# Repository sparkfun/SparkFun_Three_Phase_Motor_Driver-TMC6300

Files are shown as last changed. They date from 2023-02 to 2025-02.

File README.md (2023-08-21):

SparkFun 3-Phase BLDC Motor Driver - TMC6300
========================================

SparkFun 3-Phase BLDC Motor Driver - TMC6300 (https://www.sparkfun.com/products/21867)

[*SparkFun 3-Phase BLDC Motor Driver - TMC6300 (ROB-21867)*](https://www.sparkfun.com/products/21867)

The TMC6300 from [ADI + Trinamic](https://www.trinamic.com/) is a powerful and easy to use three phase motor driver that was designed to control our [Brushless Gimbal Motor](https://www.sparkfun.com/products/20441). However, it can be used to control any 3-phase [BLDC](https://en.wikipedia.org/wiki/Brushless_DC_electric_motor "brushless DC") or [PMSM](https://en.wikipedia.org/wiki/Synchronous_motor#Permanent-magnet "permanent magnet synchronous motor") motor with up to 2A (1.4A<sub>RMS</sub>) of total drive current. Separate high-side and low-side control of the three half-bridges allows for incredible control of each phase of the [motor commutation](https://fab.cba.mit.edu/classes/865.21/topics/power_electronics/commutation/#bldc-commutation). The driver also provides temperature and short circuit protections; and a diagnostic output to indicate system faults. With a 1.8V regulated power output and an operating voltage down to 2V, the TMC6300 is suitable for low-power microcontroller and battery powered designs (min. 2 AA/NiMh cells, or 1-2 Li-Ion cells).

Our board layout has been designed with the LEDs and labels facing up, IC down. This allows the thermal pad on the board to be access if cooling is required. Additionally, the breakout pins are specially aligned to fit perfectly onto a breadboard and hold the headers more perpendicular to facilitate assembly.

Controlling 3-phase motors is not trivial and this board requires 6 PWM signals to fully control one motor. We've found the [*Arduino Simple Field Oriented Control*](https://docs.simplefoc.com/) library to work well with the board; however, there are some hadware limitations such as [supported microconrollers for `6PWM Mode`](https://docs.simplefoc.com/microcontrollers#supported-microcontrollers). With additional considerations, for integrating [position sensors](https://docs.simplefoc.com/position_sensors) into the feedback control loop.

Repository Contents
-------------------

* **[/docs](/docs/)** - Online documentation files
    * [arduino_examples](/docs/arduino_examples/) - Example code
    * [board_files](/docs/board_files/) - Files for the product design
            * [Eagle design files](/docs/board_files/eagle_files.zip) (.zip)
            * [Schematic](/docs/board_files/schematic.pdf) (.pdf)
            * [Dimensions](/docs/board_files/dimensions.pdf) (.pdf)
    * [component_documentation](/docs/component_documentation/) - Datasheets for hardware components
    * [img/hookup_guide/](/docs/img/hookup_guide/) - Images for hookup guide documentation
* **[/Hardware](/Hardware/)** - Eagle design files (.brd, .sch)

Documentation
--------------
* **[Hookup Guide (mkdocs)](http://docs.sparkfun.com/SparkFun_Three_Phase_Motor_Driver-TMC6300/)** - Hookup guide for the TMC6300 Motor Driver hosted by GitHub pages.

*Need to download or print our hookup guide?*

* [Print *(Print to PDF)* from Single-Page View](http://docs.sparkfun.com/SparkFun_Three_Phase_Motor_Driver-TMC6300/single_page)
* [Download PDF](http://docs.sparkfun.com/SparkFun_Three_Phase_Motor_Driver-TMC6300/board_files/hookup_guide.pdf) *(Beta - Mostly works, but some attributes may be broken.)*

Product Variants
----------------
* [ROB-21867](https://www.sparkfun.com/products/21867)- v1.0, Initial Release

Version History
---------------
* [v01](https://github.com/sparkfun/SparkFun_Three_Phase_Motor_Driver-TMC6300/releases/tag/v10) - Initial Release

License Information
-------------------

This product is _**open source**_! 

Please review the LICENSE.md file for license information. 

If you have any questions or concerns about licensing, please contact technical support on our [SparkFun forums](https://forum.sparkfun.com/viewforum.php?f=152).

Distributed as-is; no warranty is given.

- Your friends at SparkFun.

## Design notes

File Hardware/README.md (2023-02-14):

SparkFun <PRODUCT NAME> Design Files
=====================================

The .sch and .brd files hare are Eagle CAD schematic and PCB design files from SparkFun Electronics.
A freeware version of Autodesk Eagle can be found [here](https://www.autodesk.com/products/eagle/free-download).

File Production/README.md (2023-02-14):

SparkFun <PRODUCT NAME> Production Files
=========================================

These are the production files SparkFun uses for printing PCBs.

License Information
-------------------
This product is open source! 

The hardware is released under [Creative Commons ShareAlike 4.0 International](https://creativecommons.org/licenses/by-sa/4.0/).

Please use, reuse, and modify these files as you see fit. Please maintain attribution to SparkFun Electronics and release anything derivative under the same license.

Distributed as-is; no warranty is given.

- Your friends at SparkFun.

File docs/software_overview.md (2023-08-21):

---
icon: simple/arduino
---

## Arduino IDE
!!! tip
	For first-time users, who have never programmed before and are looking to use the Arduino IDE, we recommend beginning with the <a href="https://www.sparkfun.com/products/15631">SparkFun Inventor's Kit (SIK)</a>, which is designed to help users get started programming with the Arduino IDE.

Most users may already be familiar with the Arduino IDE and its use. However, for those of you who have never heard the name *Arduino* before, feel free to check out the [Arduino website](https://www.arduino.cc/en/Guide/HomePage). To get started with using the Arduino IDE, check out our tutorials below:

<table class="pdf" style="border-style:none" align="center">
	<tr>
		<td align="center">
			<a class="thumb" href="https://learn.sparkfun.com/tutorials/50">
				What is an Arduino?
				<h3 class="title">What is an Arduino?</h3>
			</a>
		</td>
		<td align="center">
			<a class="thumb" href="https://learn.sparkfun.com/tutorials/61">
				Installing Arduino IDE
				<h3 class="title">Installing Arduino IDE</h3>
			</a>
		</td>
		<td align="center">
			<a class="thumb" href="https://learn.sparkfun.com/tutorials/15">
				Installing an Arduino Library
				<h3 class="title">Installing an Arduino Library</h3>
			</a>
		</td>
		<td align="center">
			<a class="thumb" href="https://learn.sparkfun.com/tutorials/1265">
				Installing Board Definitions in the Arduino IDE
				<h3 class="title">Installing Board Definitions in the Arduino IDE</h3>
			</a>
		</td>
	</tr>
</table>

<div class="grid cards" markdown align="center">

-   <a href="https://learn.sparkfun.com/tutorials/50"><figure markdown>
	What is an Arduino?
	</figure>

	---

	**What is an Arduino?**</a>

-   <a href="https://learn.sparkfun.com/tutorials/61"><figure markdown>
	Installing the Arduino IDE
	</figure>

	---
	
	**Installing the Arduino IDE**</a>

-   <a href="https://learn.sparkfun.com/tutorials/15"><figure markdown>
	Installing an Arduino Library
	</figure>

	---
	
	**Installing an Arduino Library**</a>

-   <a href="https://learn.sparkfun.com/tutorials/1265"><figure markdown>
	Installing Board Definitions in the Arduino IDE
	</figure>

	---
	
	**Installing Board Definitions in the Arduino IDE**</a>
</div>

??? tip "Need help setting up the RedBoard Plus?"
	### RedBoard Plus
	The following instructions should help users get started with the RedBoard Plus. For more information about the board, please check out our hookup guide below:

	<figure markdown>
	RedBoard Plus Hookup Guide (https://learn.sparkfun.com/tutorials/1758)
	<figcaption markdown>[**RedBoard Plus Hookup Guide**](https://learn.sparkfun.com/tutorials/1758)</figcaption>
	</figure>

	#### CH340 Driver
	Users will need to install the appropriate driver for their computer to recognize the serial-to-UART chip on their board/adapter. Most of the latest operating systems will recognize the CH340C chip on the board and automatically install the required driver.

	*To manually install the CH340 driver on their computer, users can download it from the [WCH website](http://www.wch-ic.com/products/CH340.html?). For more information, check out our [How to Install CH340 Drivers Tutorial](https://www.sparkfun.com/ch340).*

	<figure markdown>
	How to Install CH340 Drivers (https://learn.sparkfun.com/tutorials/908)
	<figcaption markdown>[**How to Install CH340 Drivers**](https://learn.sparkfun.com/tutorials/908)</figcaption>
	</figure>

	#### Arduino IDE
	When selecting a board to program in the Arduino IDE, users should select the **Arduino Uno** from the **Tools** drop-down menu _(_i.e. **Tools** > **Board** > **Arduino AVR Boards** > **Arduino Uno**)_.

	<figure markdown>
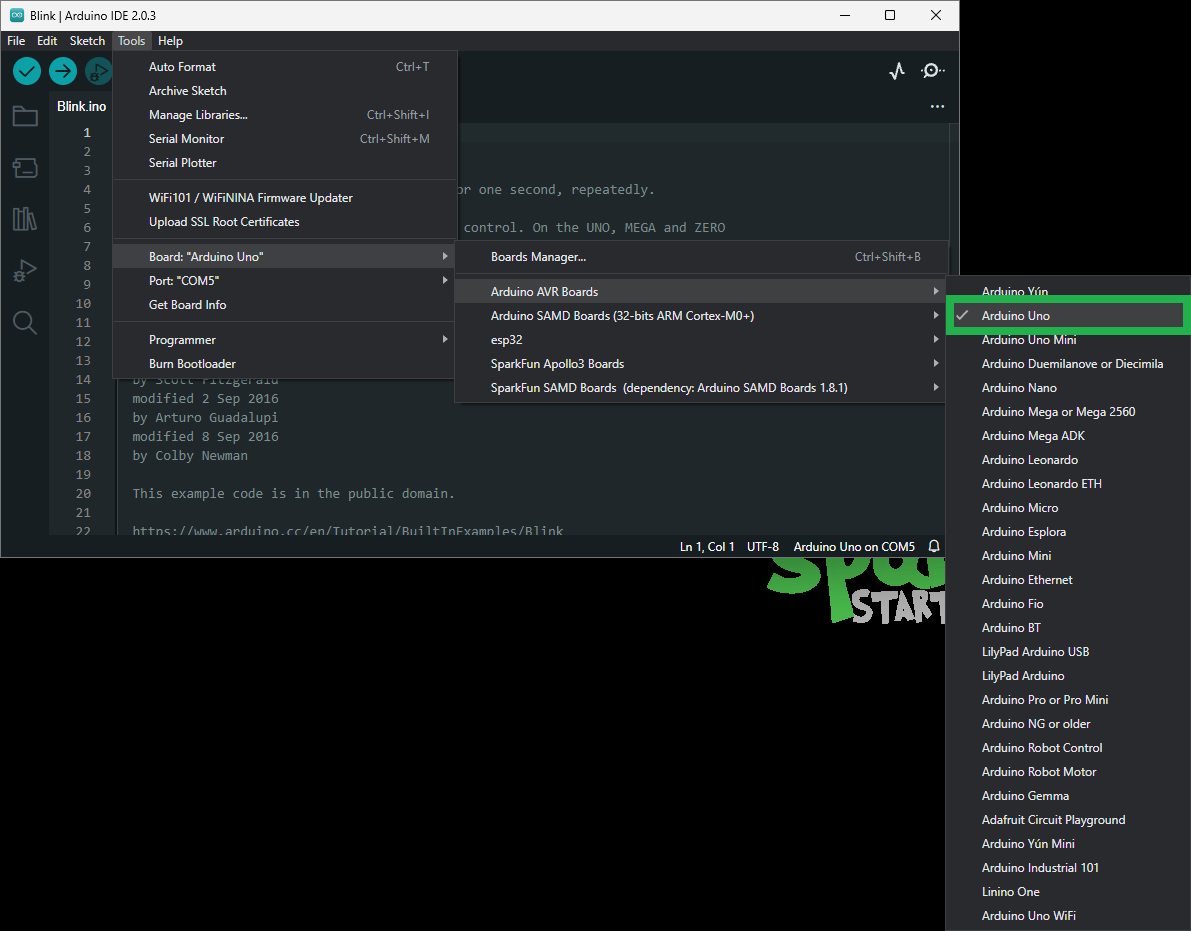
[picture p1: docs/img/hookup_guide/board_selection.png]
	
	<figcaption markdown>Select the **Arduino Uno** from the Tools drop-down menu in the Arduino IDE.</figcaption>
	</figure>

	??? info "Arduino IDE 2.x.x - *Alternative Method*"
		In the newest version of the Arduino IDE 2.`x`.`x`, users can also select their board (*green*) and port (*blue*) from the `Select Board & Port` dropdown menu (*yellow*).

		<figure markdown>
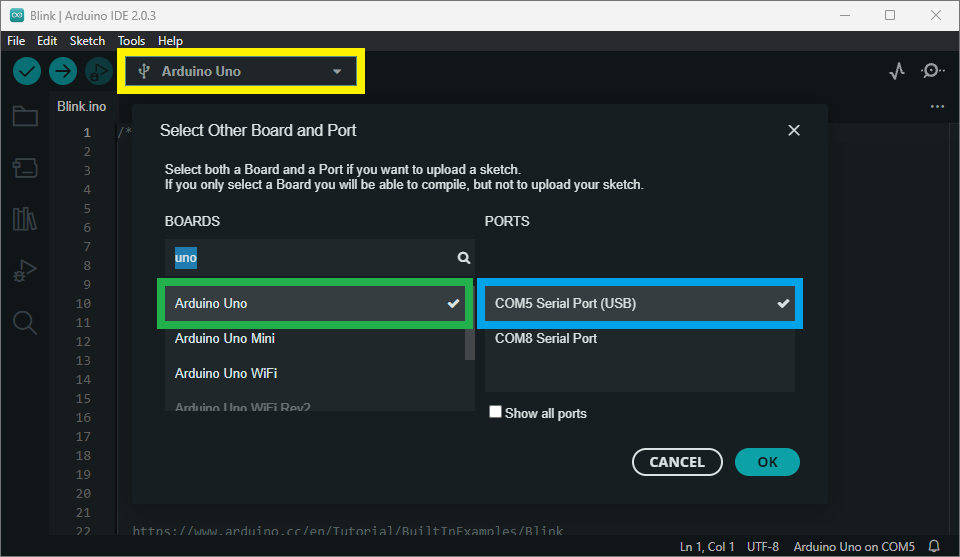
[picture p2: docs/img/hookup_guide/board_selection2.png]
		
		<figcaption markdown>Selecting the **Arduino Uno** and **COM5** port from the **Select Board & Port** drop-down menu in the Arduino IDE (v2.0.3).</figcaption>
		</figure>

## SimpleFOClibrary
The [Simple Field Oriented Control Library](https://github.com/simplefoc/Arduino-FOC) can be installed from the library manager in the Arduino IDE.

<figure markdown>
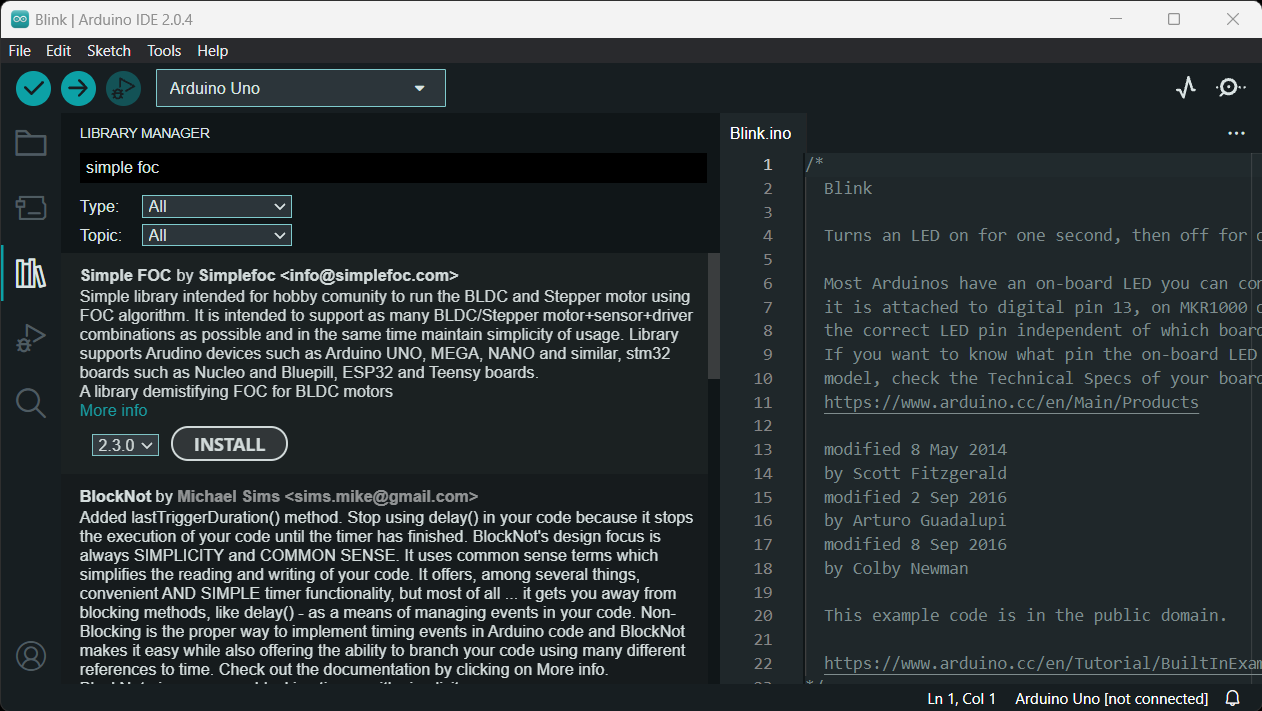
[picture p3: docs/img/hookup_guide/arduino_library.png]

<figcaption markdown>SimpleFOClibrary in the library manager of the Arduino IDE.</figcaption>
</figure>

??? tip "Arduino IDE *(v1.x.x)*"
	In the Arduino IDE v1.x.x, the library manager will have the following appearance for the SimpleFOC library:

	<figure markdown>
	Click to enlarge
	<figcaption markdown>SimpleFOClibrary in the library manager of the Arduino IDE (v1.x.x).</figcaption>
	</figure>

This library utilizes a motor control scheme called field oriented control (FOC), which can utilize a feedback control loop to drive a motor with a higher power efficiency and precision characteristics, like evenly distributed torque control.

!!! info
	For more details about the library, check out the [online documentation](https://docs.simplefoc.com/).

!!! note "Supported Hardware"
	For a detailed and up-to-date list of the hardware supported by this library, check out the [library's documentation](https://docs.simplefoc.com/supported_hardware). The following are excerpts taken from the library's documentation page:

	=== "Microcontrollers"

		--8<-- "https://raw.githubusercontent.com/simplefoc/simplefoc.github.io/master/docs/simplefoc_library/hardware/mcus/index.md:14:15"

		--8<-- "https://raw.githubusercontent.com/simplefoc/simplefoc.github.io/master/docs/simplefoc_library/hardware/mcus/index.md:35:49"

		!!! info
			For more details, please refer to the [SimpleFOC Arduino library documentation](https://docs.simplefoc.com/microcontrollers).
	
	=== "Motor Drivers"

		--8<-- "https://raw.githubusercontent.com/simplefoc/simplefoc.github.io/master/docs/simplefoc_library/hardware/drivers/index.md:19:23"

		??? warning "Current Limitations"
			--8<-- "https://raw.githubusercontent.com/simplefoc/simplefoc.github.io/master/docs/simplefoc_library/hardware/drivers/index.md:30"

		!!! tip
			While the TMC6300 isn't directly listed as part of the supported hardware for the SimpleFOC Arduino library, we have verified that is compatible with the library.

		!!! info
			For more details, please refer to the [SimpleFOC Arduino library documentation](https://docs.simplefoc.com/bldc_drivers).

	=== "Motors"

		Arduino SimpleFOClibrary supports two types of BLDC motors:

		- BLDC motors
			- 3 phase (3 wire):

				??? info "Gimbal Motors"
					--8<-- "https://raw.githubusercontent.com/simplefoc/simplefoc.github.io/master/docs/simplefoc_library/hardware/motors/BLDC_motors.md:20:22"

					--8<-- "https://raw.githubusercontent.com/simplefoc/simplefoc.github.io/master/docs/simplefoc_library/hardware/motors/BLDC_motors.md:23:28"

				??? info "High-performance Motors"		
					--8<-- "https://raw.githubusercontent.com/simplefoc/simplefoc.github.io/master/docs/simplefoc_library/hardware/motors/BLDC_motors.md:43:43"
		- Stepper motors
			- 2 phase (4 wire)
	
		??? warning "Current Limitations"
			--8<-- "https://raw.githubusercontent.com/simplefoc/simplefoc.github.io/master/docs/simplefoc_library/hardware/motors/index.md:28"

		!!! info
			For more details, please refer to the [SimpleFOC Arduino library documentation](https://docs.simplefoc.com/bldc_motors).

### 6PWM Motor Driver

Users will need to utilize the [`BLDCDriver6PWM` class](https://docs.simplefoc.com/bldcdriver6pwm) to provide the six PWM signals required for the TMC6300 motor driver.

`BLDCDriver6PWM`

:   This class provides an abstraction layer for most of the common BLDC drivers, which require six PWM signals. This method offers more control than a three PWM motor drivers, since each of the 6 half-bridges MOSFETs can be controlled independently.

	--8<-- "https://raw.githubusercontent.com/simplefoc/simplefoc.github.io/master/docs/simplefoc_library/code/drivers/bldc_driver/bldc_driver_6pwm.md:28:36"

	!!! note "Microcontroller Considerations"
		=== "Arduino Uno"
			--8<-- "https://raw.githubusercontent.com/simplefoc/simplefoc.github.io/master/docs/simplefoc_library/code/drivers/bldc_driver/bldc_driver_6pwm.md:42:50"

		=== "STM32"
			--8<-- "https://raw.githubusercontent.com/simplefoc/simplefoc.github.io/master/docs/simplefoc_library/code/drivers/bldc_driver/bldc_driver_6pwm.md:54:54"

			--8<-- "https://raw.githubusercontent.com/simplefoc/simplefoc.github.io/master/docs/simplefoc_library/code/drivers/bldc_driver/bldc_driver_6pwm.md:55:56"

			<div class="grid cards" markdown>

			-   **Hardware PWM**

				---

				--8<-- "https://raw.githubusercontent.com/simplefoc/simplefoc.github.io/master/docs/simplefoc_library/code/drivers/bldc_driver/bldc_driver_6pwm.md:59:69"

			-   **Software PWM**

				---

				--8<-- "https://raw.githubusercontent.com/simplefoc/simplefoc.github.io/master/docs/simplefoc_library/code/drivers/bldc_driver/bldc_driver_6pwm.md:72:93"

			</div>

		=== "ESP32"
			--8<-- "https://raw.githubusercontent.com/simplefoc/simplefoc.github.io/master/docs/simplefoc_library/code/drivers/bldc_driver/bldc_driver_6pwm.md:96:96"

	!!! info
		For more details about the `BLDCDriver6PWM` class, check out the [online documentation](https://docs.simplefoc.com/bldcdriver6pwm).

<!-- 
The PWM carrier frequency used to control the motor driver can greatly affect its efficiency.

* Low frequency - poor current shape, which increased heating and harmonics loss in the motor
* High frequency - increased transistor switching loss -->

### BLDC Motor

All BLDC motors are handled with the [`BLDCMotor` class](https://docs.simplefoc.com/bldcmotor).

`BLDCMotor`

:   This class implements the BLDC FOC algorithm, motion control loops, and monitoring.

	--8<-- "https://raw.githubusercontent.com/simplefoc/simplefoc.github.io/master/docs/simplefoc_library/code/motors/bldc_motors.md:23:30"

	!!! note "Motor Considerations"
		While, the datasheet for our [gimbal motor](https://www.sparkfun.com/products/20441), indicates that there are **8 pole pairs**, we have found that the motor operates more smoothly if the `BLDCMotor` class is instantiated with **7 pole pairs** instead.

		```cp
		BLDCMotor motor = BLDCMotor(7);
		```

	!!! info
		For more details about the `BLDCMotor` class, check out the [online documentation](https://docs.simplefoc.com/bldcmotor).

### Motion Control

Unless a feedback loop is incorporated when driving the motor *(i.e. with [position sensors](https://docs.simplefoc.com/sensors) or [current sensing](https://docs.simplefoc.com/current_sense))*, users should implement the SimpleFOC library using the [open-loop control](https://docs.simplefoc.com/open_loop_motion_control).

Open-Loop Motion Control Types:

* [Velocity](https://docs.simplefoc.com/velocity_openloop)
* [Position](https://docs.simplefoc.com/angle_openloop)

<!-- #### Sensorless FOC
Current measurement

#### Closed-Loop
With position sensors

Control Types (available in library):
* Torque
* Velocity
* Angle

#### Low-side current sensing

While the SimpleFOC Arduino library offers the option to incorporate low-side current sensors into the feedback loop, 

--8<-- "https://raw.githubusercontent.com/simplefoc/simplefoc.github.io/master/docs/simplefoc_library/code/drivers/bldc_driver/bldc_driver_6pwm.md:101:110"

utilizing the [open loop example](https://github.com/simplefoc/Arduino-FOC/blob/master/examples/motion_control/open_loop_motor_control/open_loop_velocity_example/open_loop_velocity_example.ino) combined with the [6 channel PWM method](https://docs.simplefoc.com/bldcdriver6pwm) and *every* PWM pin on the Arduino Uno gets this board working. Note the [pairs of PWM pins](https://docs.simplefoc.com/bldcdriver6pwm) that must be used. -->

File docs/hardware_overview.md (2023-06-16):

---
icon: material/cog
---

## Board Dimensions

The board dimensions are illustrated in the drawing below; the listed measurements are in inches.

<figure markdown>
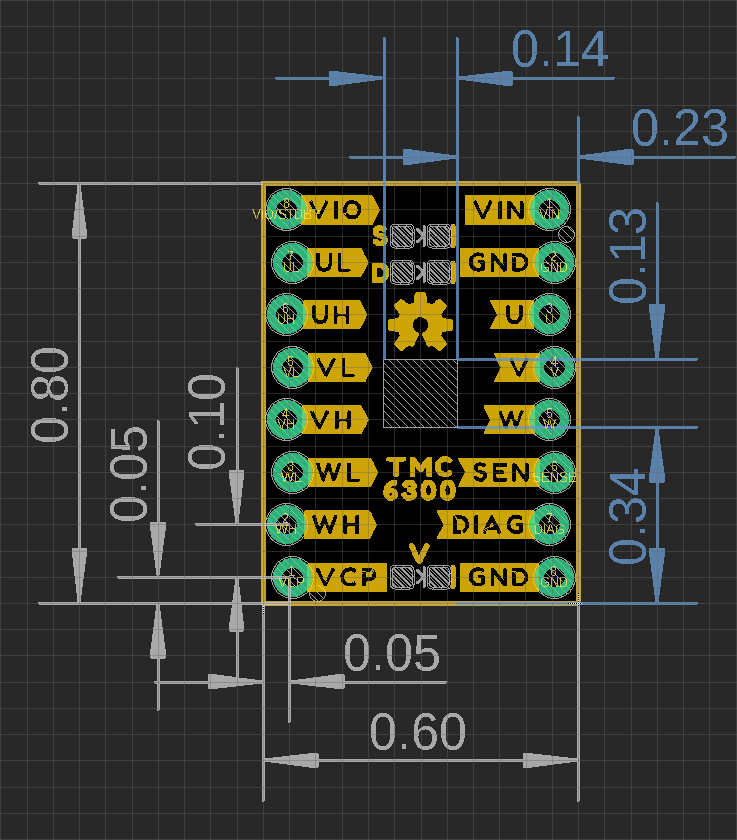
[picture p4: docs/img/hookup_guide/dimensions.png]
Board Dimensions

<figcaption markdown>
[Board dimensions (PDF)](../board_files/dimensions.pdf) for the TMC6300 motor driver breakout board, in inches.
</figcaption>
</figure>

??? tip "Need more measurements?"
	For more information about the board's dimensions, users can download the [eagle files](../board_files/eagle_files.zip) for the board. These files can be opened in Eagle and additional measurements can be made with the dimensions tool.

	??? info ":octicons-download-16:{ .heart } Eagle - Free Download!"
		Eagle is a [CAD]("computer-aided design") program for electronics that is free to use for hobbyists and students. However, it does require an account registration to utilize the software.

		<center>
		[Download from<br>:autodesk-primary:{ .autodesk }](https://www.autodesk.com/products/eagle/free-download "Go to downloads page"){ .md-button .md-button--primary width="250px" }
		</center>
	
	??? info ":straight_ruler: Dimensions Tool"
		This video from Autodesk demonstrates how to utilize the dimensions tool in Eagle, to include additional measurements:

		<center>
		<div class="video">
		<iframe src="https://www.youtube.com/embed/dZLNd1FtNB8" title="EAGLE Dimension Tool" frameborder="0" allow="accelerometer; autoplay; clipboard-write; encrypted-media; gyroscope; picture-in-picture" allowfullscreen></iframe>
		</div>
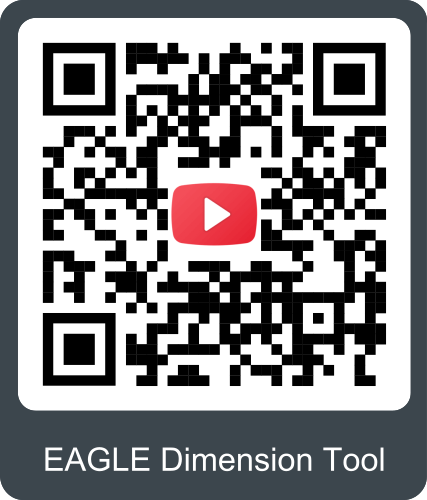
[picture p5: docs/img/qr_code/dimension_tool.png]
QR code to play video
		
		</center>

## Power

Users are provided with [PTH](https://en.wikipedia.org/wiki/Through-hole_technology "Plated Through Holes") to connect their external power supply, I/O logic-level voltage, and the regulated 1.8V output. The TMC6300 motor driver has an input voltage range of **2.0V** to **11.0V**.

<figure markdown>
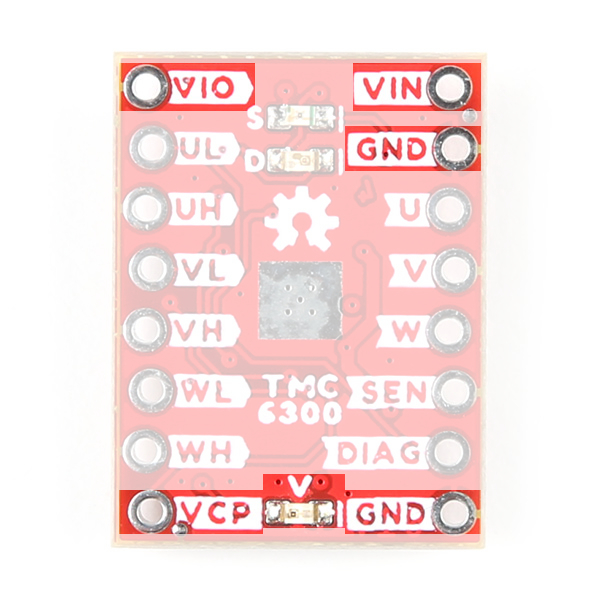
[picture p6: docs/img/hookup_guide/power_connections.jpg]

<figcaption markdown>
The power connections on the TMC6300 motor driver.
</figcaption>
</figure>

Below, is a general summary of the circuitry on the board:

* **`VIN`** - Power supply input
    * Range: **2 to 11V**
* **`VIO`** - I/O supply voltage
	* Range: **1.8 to 5.25V**
	* `NSTDBY` - IC goes to standby mode and resets when this pin is pulled to `GND`
* **`VCP`** - Charge pump voltage
* **`GND`** - The common ground or the 0V reference for the board

!!! info
	For more details, users can reference the [schematic](../board_files/schematic.pdf) and the [TMC6300 datasheets](../component_documentation/TMC6300.pdf).

??? caution "Motor Voltage"
	Even though the input voltage range for the motor driver goes down to 2V, users will need to provide the minimum operating voltage for their motor. *Our [Gimbal Stabilizer Motor](https://cdn.sparkfun.com/assets/e/b/2/8/3/OT-EM3215_DC_Brushless_Gimbal_Motor_3_Phase_Datasheet.pdf) has an operating voltage range of 6 - 8V.*

### Power LED

The red, power (`PWR`) LED will light up when a power supply is connected to the board. However, the LED can be disabled for low-power applications by cutting the [jumper](#jumper).

<figure markdown>
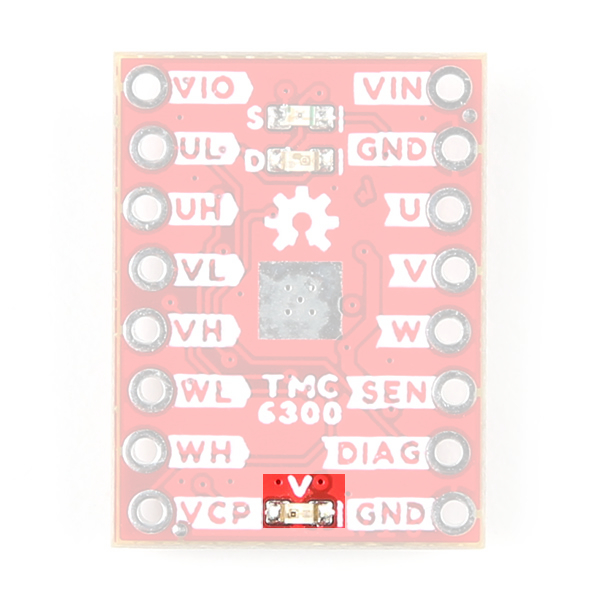
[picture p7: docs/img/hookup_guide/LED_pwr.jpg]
Power LED

<figcaption markdown>
The `PWR` status LED indicator for the TMC6300 motor driver.
</figcaption>
</figure>

### `VIO`/Standby Pin

In it's default configuration, the `VIO` pin is used to enable the motor driver and set the logic level voltage (**1.8** to **5.25V**) for the I/O pins. However, the `VIO` pin also operates as a standby pin when it is pulled `LOW`. In standby, the TMC6300 resets and sits in standby mode.

<figure markdown>
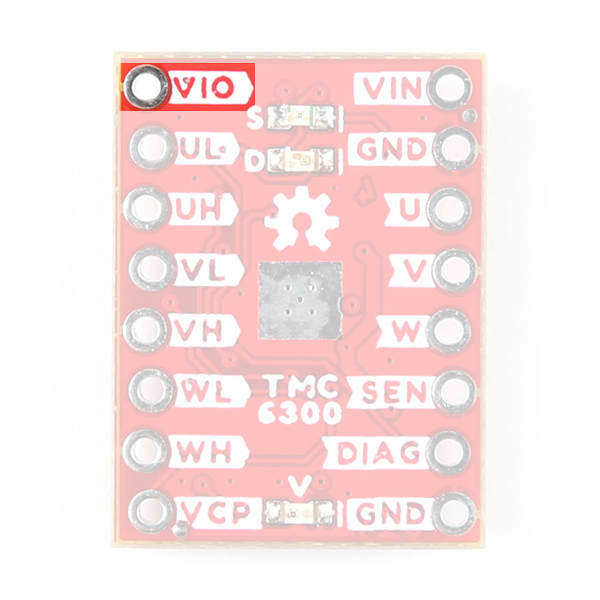
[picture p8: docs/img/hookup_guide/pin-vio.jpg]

<figcaption markdown>
`VIO` pin on the TMC6300 motor driver.
</figcaption>
</figure>

### `VCP`&nbsp;Pin

The `VCP` pin is broken out for users to include an external charge pump capacitor. Adding an external capacitor would help stabilize the supply voltage, from the large voltage swings (dV/dt) of the motor driver's operation. A 1nF to 100nF capacitor rated at 10V, is recommended by the [datasheet](./component_documentation/TMC6300.pdf).

<figure markdown>
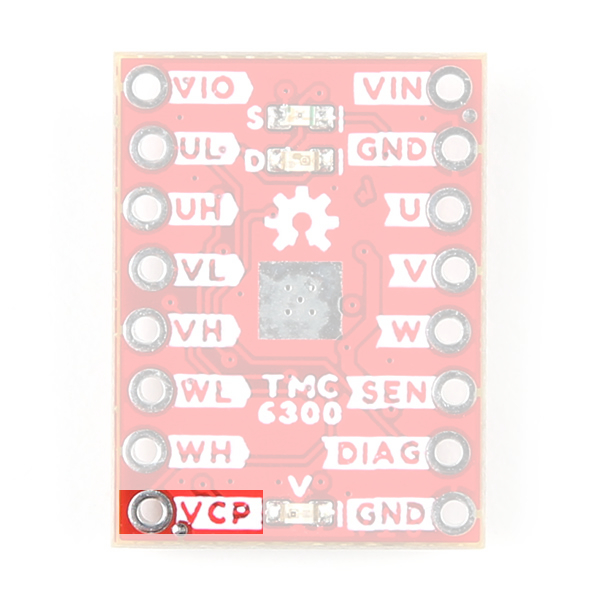
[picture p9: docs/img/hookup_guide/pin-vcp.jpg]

<figcaption markdown>
`VCP` pin on the TMC6300 motor driver.
</figcaption>
</figure>

## :fontawesome-solid-microchip:&nbsp;TMC6300

The [TMC6300](../component_documentation/TMC6300.pdf) from [Trinamic Motion Control](https://www.trinamic.com/), part of Analog Devices, is a low voltage, 3-Phase [BLDC](https://en.wikipedia.org/wiki/Brushless_DC_electric_motor "Brushless DC")/[PMSM](https://en.wikipedia.org/wiki/Synchronous_motor#Permanent-magnet "Permanent-Magnet Synchronous Motor") motor driver utilizing separate high-side and low-side control signals for its three half-bridges.

<center>
<table class="pdf" markdown="1">
<tr markdown="1">
<td markdown="block">
Features:

* VIN: 2.0V to 11.0V
	* Operating current: 7mA
	* Standby current: 30nA
* VOUT: 1.8V
* 3 Half-Bridges
	* 3 High-side MOSFETs
	* 3 Low-side MOSFETs
* I/O Supply Voltage Input
* Diagnostic Output
* Overtemperature Protection
	* Shutdown Temperature: 150&deg;C
	* Typical Power Dissipation: 1W
* Short Protection

</td>
<td align="center">
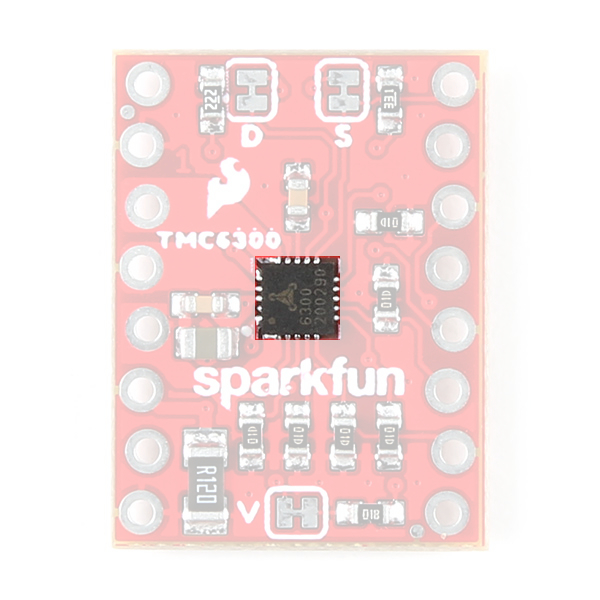
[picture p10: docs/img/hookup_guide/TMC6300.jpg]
<br>
<i>TMC6300 chip on the TMC6300 motor driver.</i>
</td>
</tr>
</table>
</center>

<div class="grid cards hide" markdown>

-   Features:

	* VIN: 2.0V to 11.0V
		* Operating current: 7mA
		* Standby current: 30nA
	* VOUT: 1.8V
	* 3 Half-Bridges
		* 3 High-side MOSFETs
		* 3 Low-side MOSFETs
	* I/O Supply Voltage Input
	* Diagnostic Output
	* Overtemperature Protection
		* Shutdown Temperature: 150&deg;C
		* Typical Power Dissipation: 1W
	* Short Protection

-	<figure markdown>
	
	<figcaption markdown>
	TMC6300 chip on the TMC6300 motor driver.
	</figcaption>
	</figure>

</div>

!!! info
	For more details, please refer to the [TMC6300 datasheet](../component_documentation/TMC6300.pdf) and [application note](../component_documentation/AN_AP3428.pdf).

??? warning "Chip Protections"
	The TMC6300 features the overtemperature and short protections:

	* The overtemperature protection feature implements a two temperature thresholds; however, the datasheet warns users that this should only be relied on as an emergency percaution and may not prevent the destruction of the IC. This is due to several factors including that excess heat can generate quickly before the overtemperature sensor can react. Therefore, users should prevent this situation from occuring by design with methods such as adequate heat dissipation.
	* The short protection feature gaurds the motor commutation channels by monitoring the current flowing through each of the power stage MOSFETs. Once a short condition (short to `GND` or `VS`) is safely detected, all driver bridges become switched off, and the `DIAG` output becomes set. In order to restart the motor, the users must must disable and restart the TMC6300. As with the overtemperature protection, the datasheet warns users that this feature should only be relied on as an emergency percaution and may not prevent the destruction of the IC or detect all possible short events.

	*By monitoring the current draw through the `SEN` pin, users can also implement an over current protection scheme in their software. This can also aid in preventing a trigger in the overtemperature protection and validating a short detection.*

??? tip "Maximum Load Current"
	When pushing the maximum load current of 2A, users should monitor the current draw through the `SEN` pin and add a heat sink to provide additional heat dissipation. This should precautions can help to avoid damaging the IC.

### Motor Commutation

The TMC6300 relies on an electrical [commutation](https://fab.cba.mit.edu/classes/865.21/topics/power_electronics/commutation/#bldc-commutation) sequence/signal to drive the motor phases to a [BLDC](https://en.wikipedia.org/wiki/Brushless_DC_electric_motor "brushless DC") or [PMSM](https://en.wikipedia.org/wiki/Synchronous_motor#Permanent-magnet "permanent magnet synchronous motor") motor. The commutation signals for these motors are trapezoidal for BLDC motors and sinusoidal for PMSM motors.

<div class="grid cards" markdown>

-	<figure markdown>
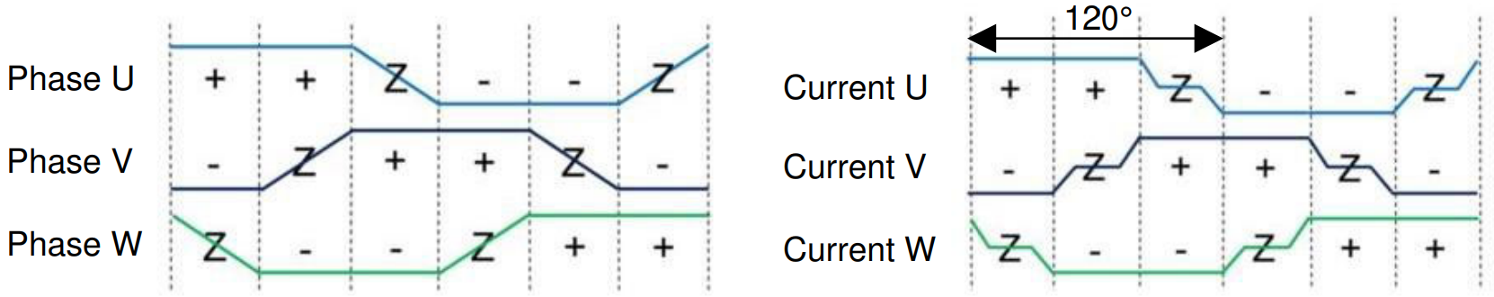
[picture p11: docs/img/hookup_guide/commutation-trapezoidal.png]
	
	<figcaption markdown>
	Trapezoidal motor commutation.
	</figcaption>
	</figure>

-	<figure markdown>
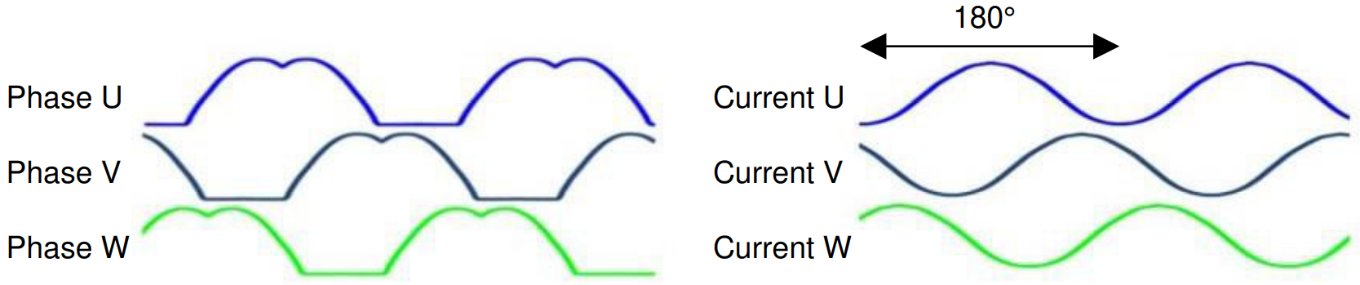
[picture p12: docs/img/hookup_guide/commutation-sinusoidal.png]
	
	<figcaption markdown>
	Sinusoidal motor commutation.
	</figcaption>
	</figure>

</div>

<center>
*(Source: [Brushless-DC Motor Driver Considerations and Selection Guide](https://www.ti.com/lit/an/slvaes1a/slvaes1a.pdf) application note)*
</center>

For a trapezoidal signal, the high-side (HS) and low-side (LS) MOSFETs, can just be driven high or low. However, in order to approximate a sinusoidal signal, a progressively varying PWM signal must be provided from the microcontroller and all six signal should be in sync with each other.

<figure markdown>

<figcaption markdown>
Sinusoidal PWM signal.<br>
(Source: [Demystifying BLDC motor commutation: Trap, Sine, & FOC](https://www.ti.com/lit/ml/slyp711/slyp711.pdf))
</figcaption>
</figure>

??? info "PMSM vs BLDC Motor"
	A BLDC motor (sometimes referred to as a BLDM) and a PMSM (sometimes referred to as an AC synchronus motor) for the most part will appear the same in their internal construction. The difference between these types of motors is in their stator windings. This means that their commutation (the electrical signals used to drive the motor) is different.

	* In a BLDC motor, the windings are concentrated on salient poles, requiring a voltage waveform that's more trapeziodal than sinusoidal.
	* In a PMSM, the windings are distributed over several poles, requiring a voltage waveform that's more more sinusoidal.

	!!! tip "Gimbal Motor"
		Based on measuring the output from one of the coils, our gimbal motor is a PMSM and would require a sinusoidal waveform to drive the motor. It should be noted that a trapezodial waveform can probably be used; however, users may notice effects such as cogging.

??? tip "Alternative Use Cases"
	While this IC is intended to be used to drive 3-Phase BLDC/PMSM motors, users can easily adapt their hardware and software to work with other moters. For example, users could use two half-bridges to form an H-bridge and adapt their control software to drive a brushed, DC motor.

## I/O Pins

There are several I/O pins for the TMC6300. Some of the pins are detailed in the [power section](#power) above; the `VOUT` pin is ommitted because it isn't broken out.

### Half-Bridges

The TMC6300 features high-side and low-side MOSFET pairs of the three available half-bridges which control the commutation of the three motor phases.

<figure markdown>
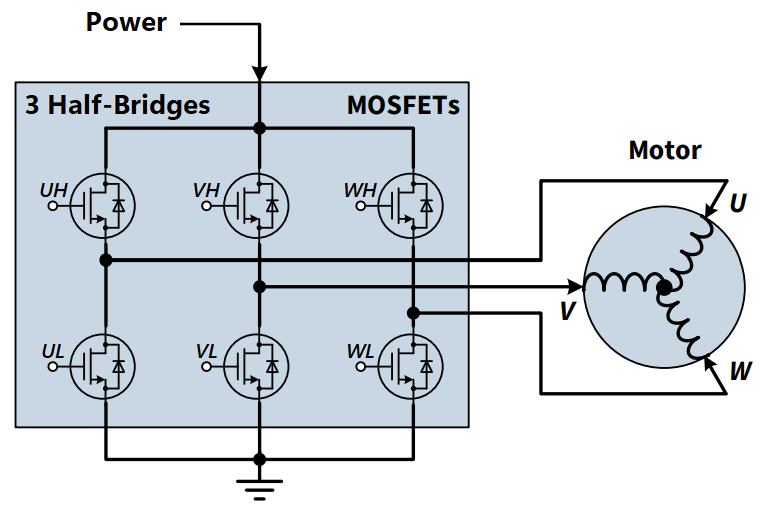
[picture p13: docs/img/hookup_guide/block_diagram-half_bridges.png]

<figcaption markdown>
6 PWM control of a 3-phase motor commutation.<br>
(Source: Modified from the [Block commutation vs. FOC in power tool motor control](https://www.infineon.com/dgdl/Infineon-Motor_power_tool_Block_Commutation_vs_FOC-ApplicationNotes-v01_00-EN.pdf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) application note)
</figcaption>
</figure>

=== "Input"
	The electronic commutation sequence of these pins will depend on the motor that is connected. For most cases, users will provide a PWM signal to each of the pins. *These are active-high pins with logic levels controlled by the `VIO` pin.*

	<figure markdown>
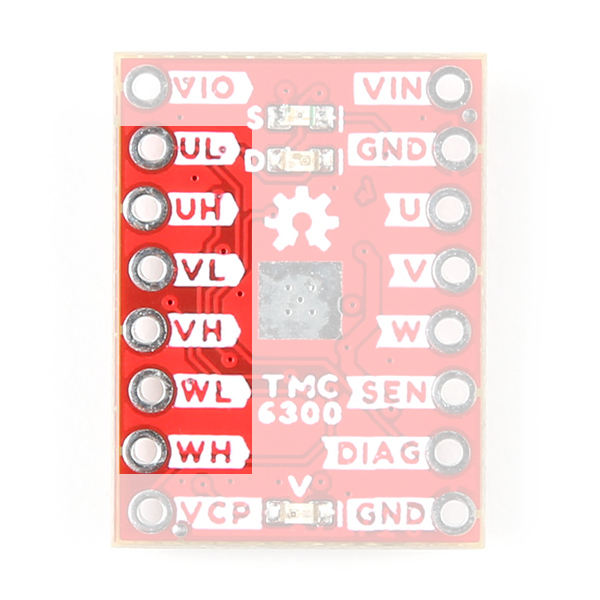
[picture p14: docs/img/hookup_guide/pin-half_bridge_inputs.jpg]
	
	<figcaption markdown>
	The six control pins (`UL`/`UH`, `VL`/`VH`, and `WL`/`WH`) for the three half-bridges of the TMC6300 motor driver.
	</figcaption>
	</figure>

	??? info "Active High"
		By pulling the pin high, the MOSFET will enable power to flow through that section of the half-bridge.
	
	??? tip "Microcontroller Limitations"
		Users will need to use pins capable of providing a PWM signal. In addition, for the recommended [Simple FOC Arduino library](https://github.com/simplefoc/Arduino-FOC), users will also need to consider the [supported microcontroller](https://docs.simplefoc.com/microcontrollers) as well as the configuration for the [6PWM mode](https://docs.simplefoc.com/bldcdriver6pwm#step-1-hardware-setup).

=== "Output"
	With the electronic commutation sequence provided to the half-bridges, the output motor phases will drive a connected motor.

	<figure markdown>
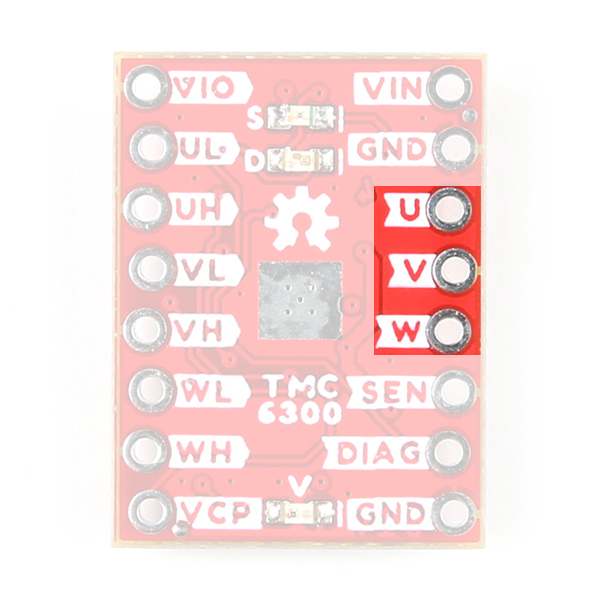
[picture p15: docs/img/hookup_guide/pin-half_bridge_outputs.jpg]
	
	<figcaption markdown>
	The three motor phase outputs (`U`/`V`/`W`) from the TMC6300, used to drive a motor.
	</figcaption>
	</figure>

	??? info "Wiring Sequence"
		For a 3-phase brushless motor, the connection sequence of the wires to a BLDC motor doesn't necessarily matter; the direction that the motor spins can be controlled through the software. However, for reference, switching two of the output channels to the motor will automatically reverse the direction that the motor was spinning.

		* If users swap the `U` and `V` connections, but leave the `W` connection alone, the motor will now spin in the opposite direction of the original configuration.

### Diagnostic Pin

The diagnostic pin is triggered based on different faults *(i.e. shorts and overtemperature)* detected by the IC. By default, the status will be indicated by the, green diagnostic, `D` LED and will remail `LOW` until triggered. Once triggered, users will need to disable and reset the TMC6300 or power cycle the board.

<figure markdown>
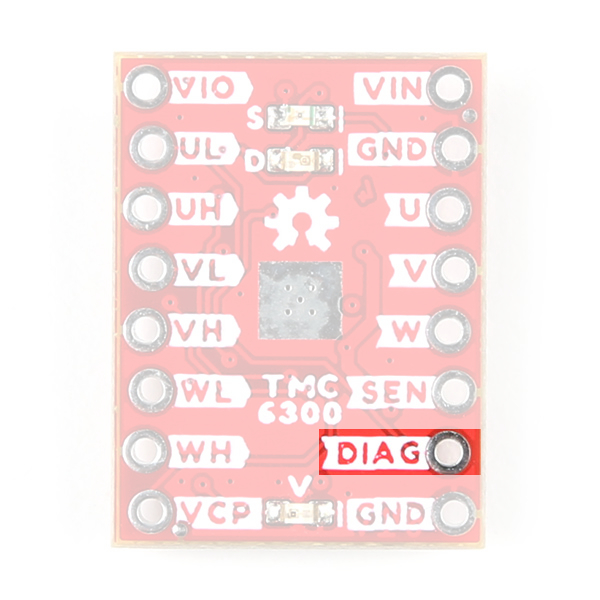
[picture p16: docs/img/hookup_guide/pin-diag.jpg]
Diagnostic Pin

<figcaption markdown>
The `DIAG` pin on the TMC6300 motor driver.
</figcaption>
</figure>

Users can also monitor the `DIAG` pin, so their microcontroller knows when to reset the TMC6300 to clear the fault.

### Current Sense Pin
The current sense pin is the foot point of the `U` and `V` half-bridges, with a 0.12&ohm; resistor attached. Users can measure the voltage across the `SENSE` and `GND` pins to determine the current flowing to the motor; however, it is recommended that an op-amp be attached to amplify the signal.

<figure markdown>
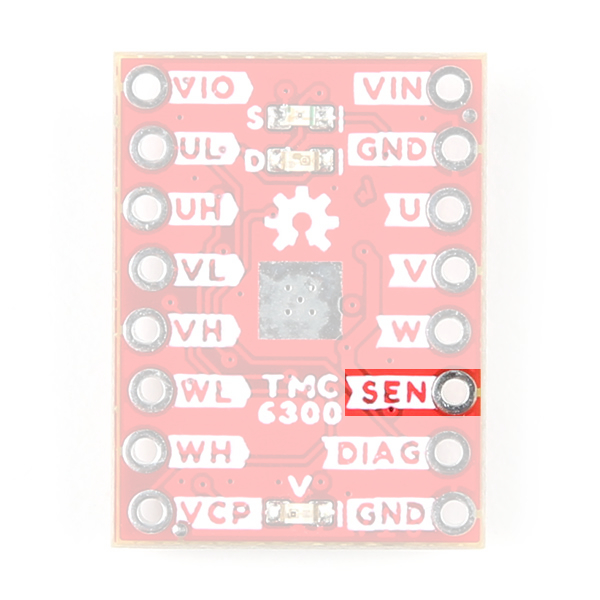
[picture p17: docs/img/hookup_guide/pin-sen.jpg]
Current Sense Pin

<figcaption markdown>
The `SEN` pin on the TMC6300 motor driver.
</figcaption>
</figure>

## LEDs

There are three status indicator LEDs on the TMC6300 motor driver:

* `V` - Power *(Red)*
	* Turns on once power is supplies to the `VIN` pin
* `D` - Diagnostics *(Green)*
	* Turns on to indicate a fault *(see [diagnostic pin](#diagnostic-pin) section)*
* `S` - Standby *(Blue)*
	* Turns on when the motor driver is enabled
	* Turns off, when the IC has been reset and the motor driver is in standby mode

<figure markdown>
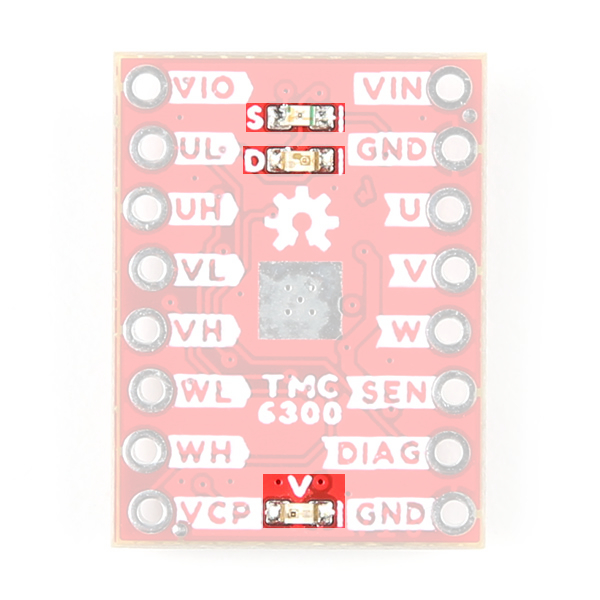
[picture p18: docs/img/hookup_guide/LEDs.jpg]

<figcaption markdown>
The status indicator LEDs on the TMC6300 motor driver.
</figcaption>
</figure>

## Heat Sink Pad

A 0.13" x 0.14" platted copper pad is provided on the top of the board, where users can add a heat sink to dissipate excess heat generated by the TMC6300. The pad can accommodate the [small heatsink](https://www.sparkfun.com/products/11510) in our catalog.

??? info "Thermal Shutdown Temperature"
	The AP329A has a 160&deg;C (320&deg;F) thermal shutdown temperature. The TMC6300 will restart automatically when the junction temperature decreases to +130°C.

??? warning "Copper Heat Sink"
	Users may be tempted to use our [copper heatsink](https://www.sparkfun.com/products/18704) on their board. However, we highly advise against using the copper heatsink because it barely fits and will likely cause a short across one of the pins.

	<figure markdown>
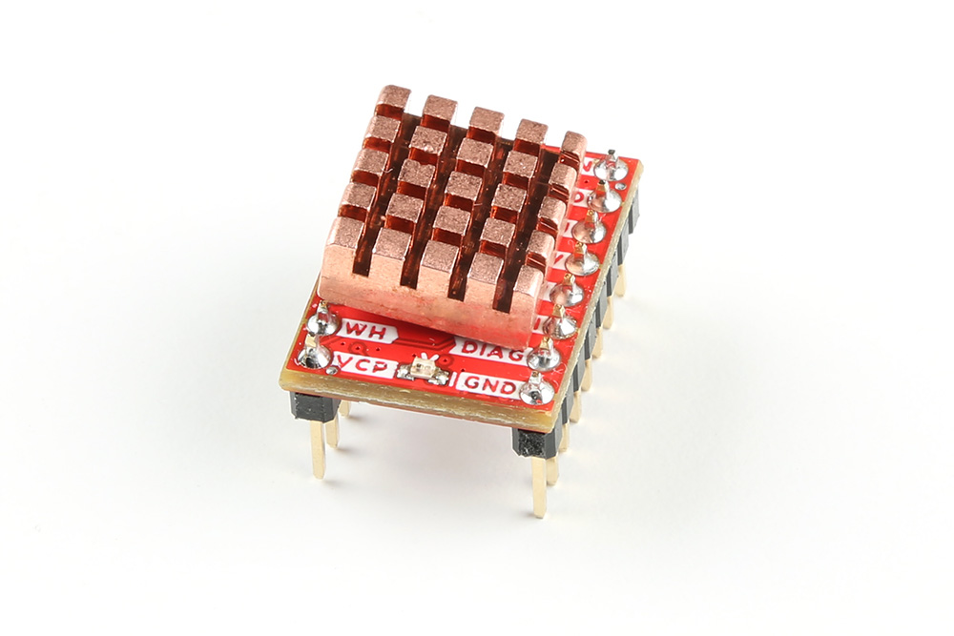
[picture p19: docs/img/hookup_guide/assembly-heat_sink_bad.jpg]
	
	<figcaption markdown>
	Copper heatsink not fitting on the TMC6300 motor driver.
	</figcaption>
	</figure>

<figure markdown>
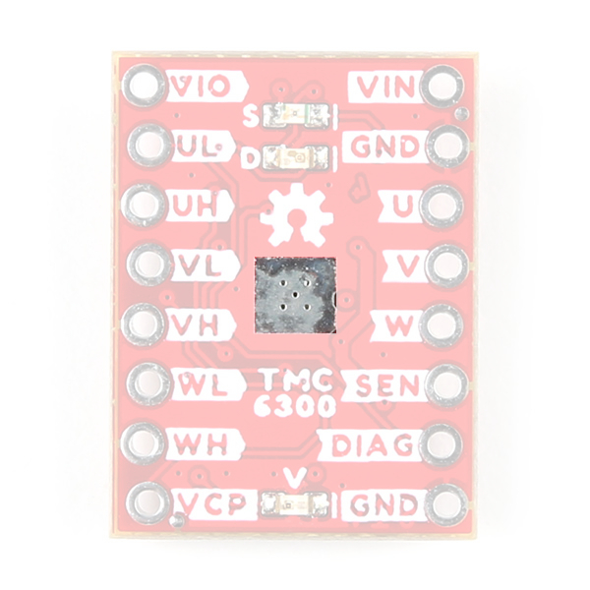
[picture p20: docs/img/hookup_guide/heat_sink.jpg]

<figcaption markdown>
Heat sink pad on the top of the TMC6300 motor driver.
</figcaption>
</figure>

## Jumpers

??? note "Never modified a jumper before?"
	Check out our <a href="https://learn.sparkfun.com/tutorials/664">Jumper Pads and PCB Traces tutorial</a> for a quick introduction!
	<p align="center">
		<a href="https://learn.sparkfun.com/tutorials/664">How to Work with Jumper Pads and PCB Traces<br>
		Tutorial's thumbnail</a>
	</p>

There are three jumpers on the back of the board that can be used to easily modify a hardware connections on the board.

* **V** - This jumper can be used to remove power from the red, power LED.
* **S** - This jumper can be used to remove power from the blue, standby LED.
* **D** - This jumper can be used to remove power from the green, diagnostic LED.

<figure markdown>
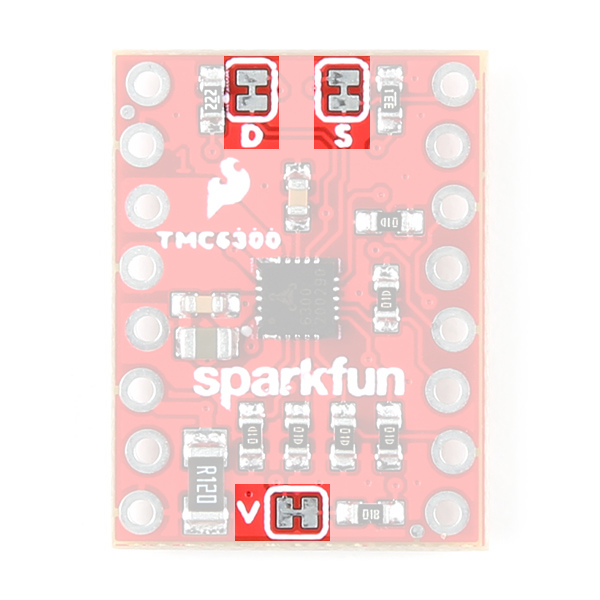
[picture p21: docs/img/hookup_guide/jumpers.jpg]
Jumpers

<figcaption markdown>
The LED jumpers on the back of the TMC6300 motor driver.
</figcaption>
</figure>

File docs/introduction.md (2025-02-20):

---
icon: material/book-open-page-variant
---

# Introduction
<div class="grid cards desc" markdown>

-   <a href="https://www.sparkfun.com/products/21867">
	**Brushless Motor Driver - 3 Phase (TMC6300)**<br>
	**SKU:** ROB-21867
	
	---
	
	<figure markdown>
	Product Thumbnail
	</figure></a>

	<center>
	<article class="video_desc">
	<iframe src="https://www.youtube.com/embed/I0sJSTlUF_E" title="Product Showcase: SparkFun Brushless Motor Driver - 3 Phase (TMC6300)" frameborder="0" allow="accelerometer; autoplay; clipboard-write; encrypted-media; gyroscope; picture-in-picture" allowfullscreen></iframe>
	</article>
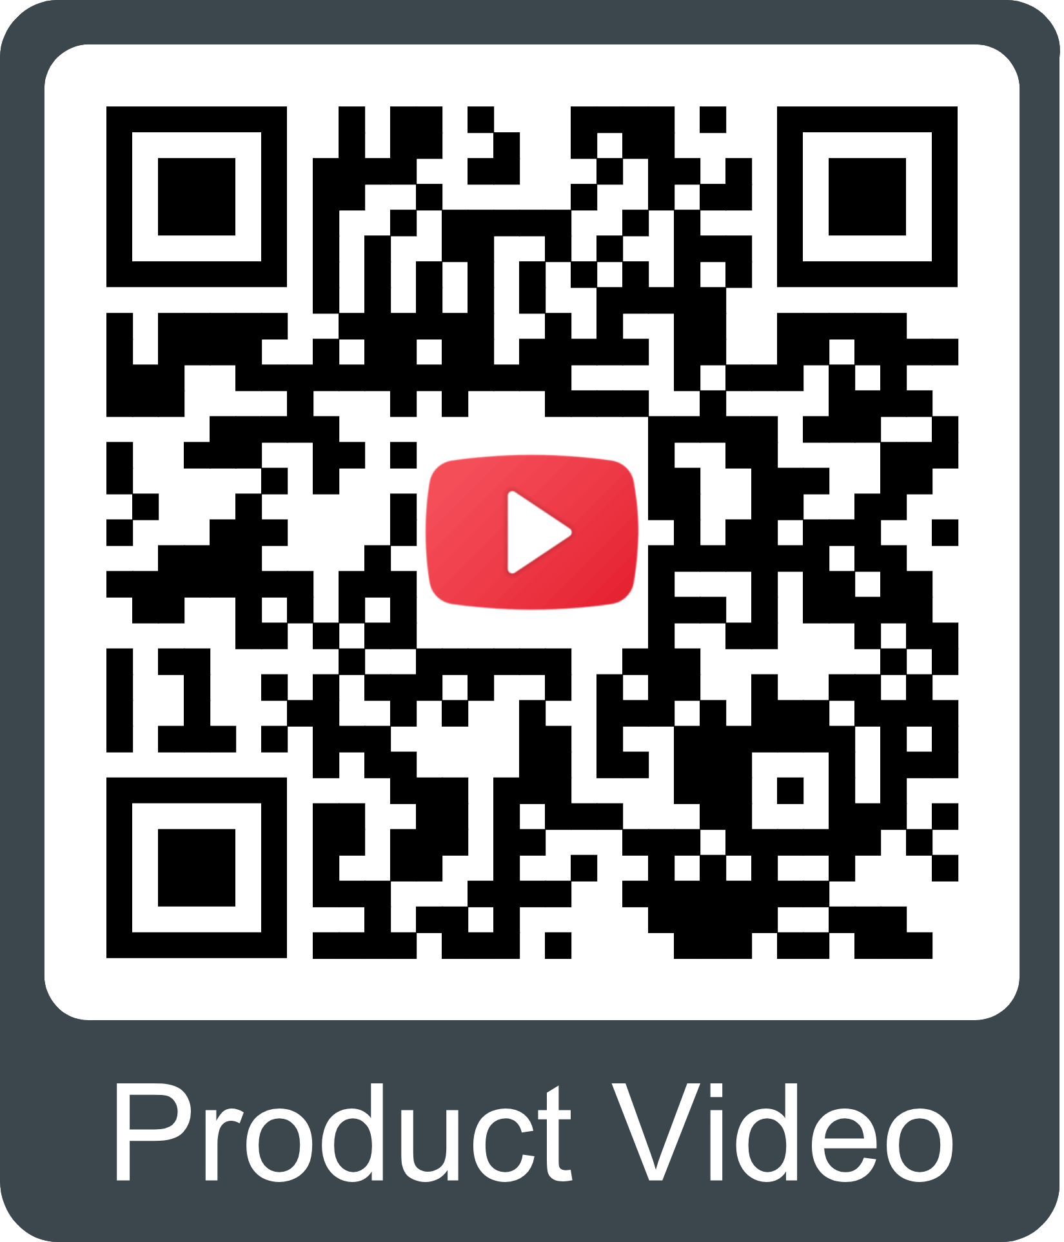
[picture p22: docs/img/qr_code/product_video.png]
QR code to play video
	
	</center>

-	The TMC6300 from [ADI + Trinamic](https://www.trinamic.com/) is a powerful and easy to use three phase motor driver that was designed to control our [Brushless Gimbal Motor](https://www.sparkfun.com/products/20441). However, it can be used to control any 3-phase [BLDC](https://en.wikipedia.org/wiki/Brushless_DC_electric_motor "brushless DC") or [PMSM](https://en.wikipedia.org/wiki/Synchronous_motor#Permanent-magnet "permanent magnet synchronous motor") motor with up to 2A (1.4A~RMS~) of total drive current. Separate high-side and low-side control of the three half-bridges allows for incredible control of each phase of the [motor commutation](https://fab.cba.mit.edu/classes/865.21/topics/power_electronics/commutation/#bldc-commutation). The driver also provides temperature and short circuit protections; and a diagnostic output to indicate system faults. With a 1.8V regulated power output and an operating voltage down to 2V, the TMC6300 is suitable for low-power microcontroller and battery powered designs (min. 2 AA/NiMh cells, or 1-2 Li-Ion cells).

	Our board layout has been designed with the LEDs and labels facing up, IC down. This allows the thermal pad on the board to be access if cooling is required. Additionally, the breakout pins are specially aligned to fit perfectly onto a breadboard and hold the headers more perpendicular to facilitate assembly.

	Controlling 3-phase motors is not trivial and this board requires 6 PWM signals to fully control one motor. We've found the [*Arduino Simple Field Oriented Control*](https://docs.simplefoc.com/) library to work well with the board; however, there are some hadware limitations such as [supported microconrollers for `6PWM Mode`](https://docs.simplefoc.com/microcontrollers#supported-microcontrollers). With additional considerations, for integrating [position sensors](https://docs.simplefoc.com/position_sensors) into the feedback control loop.

	<center>
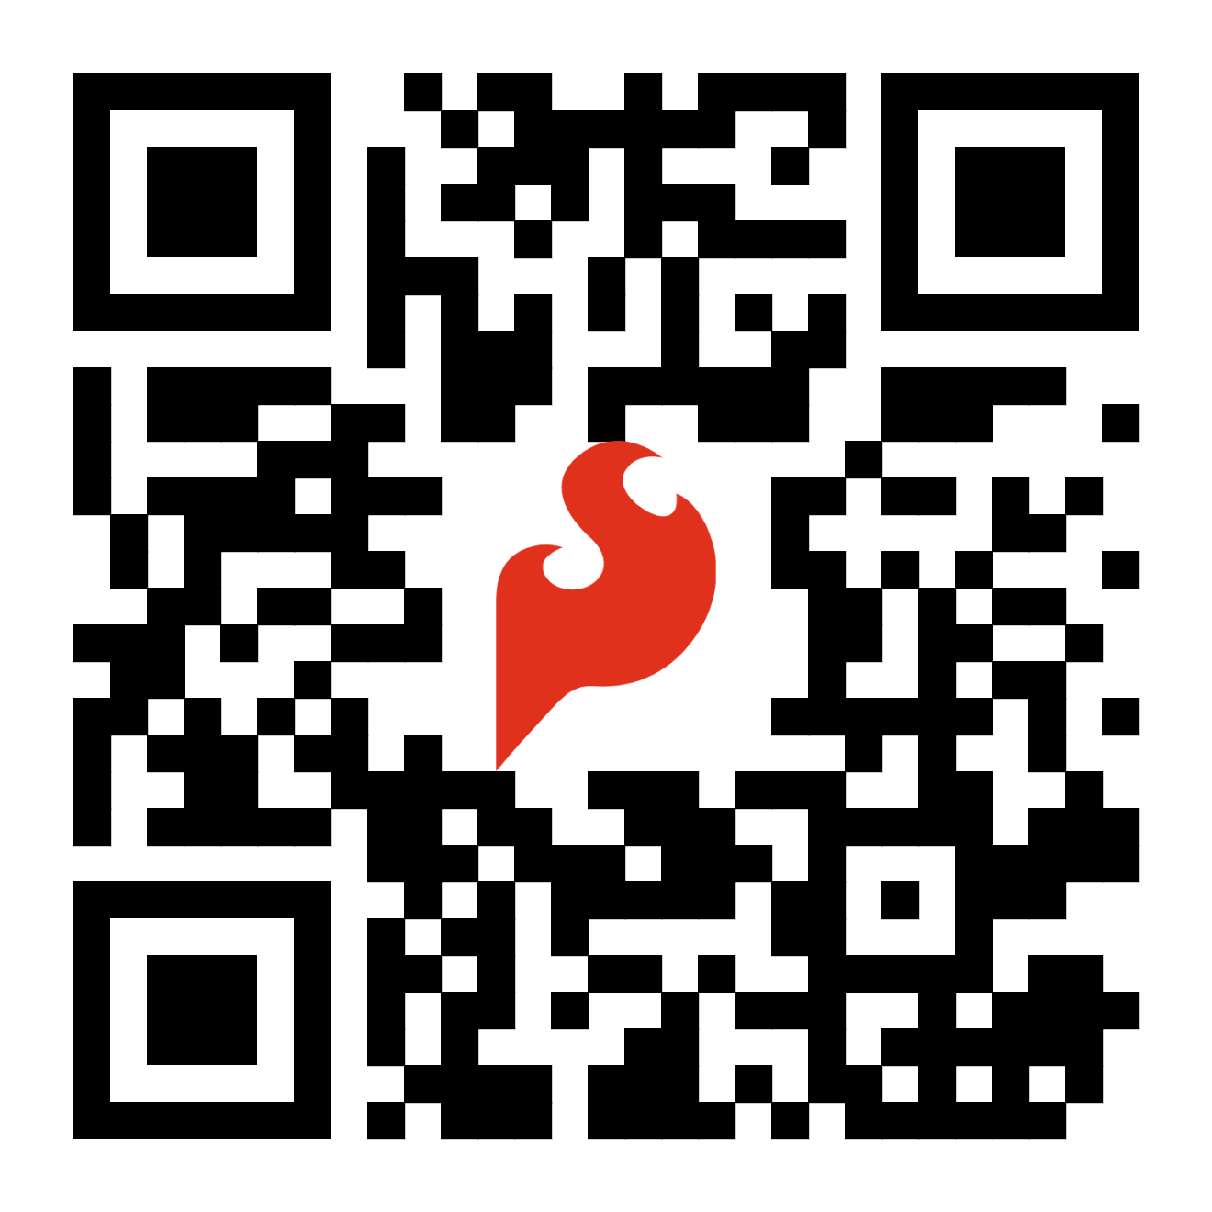
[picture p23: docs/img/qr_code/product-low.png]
QR code to product page
	[&nbsp;&nbsp;&nbsp;Purchase from SparkFun :fontawesome-solid-cart-plus:{ .heart }](https://www.sparkfun.com/products/21867){ .md-button .md-button--primary }
	</center>

</div>

## :fontawesome-solid-list-check:&nbsp;Required Materials
To get started, users will need a few items. Now some users may already have a few of these items, feel free to modify your cart accordingly.

* Computer with an operating system (OS) that is compatible with all the software installation requirements.
* A compatible microcontroller/Arduino board; we recommend the [SparkFun RedBoard Plus](https://www.sparkfun.com/products/18158).

	!!! warning
		The recommended Arduino library for the TMC6300 motor driver is not compatible with all microcontrollers or boards. For a complete list of compatible microcontrollers and boards, please refer to the [documentation](https://github.com/simplefoc/Arduino-FOC#boards) for the Simple Field Oriented Control Library.

* [USB 3.1 Cable A to C - 3 Foot](https://www.sparkfun.com/products/14743) - Used to interface with the RedBoard Plus (1)
{ .annotate }

	1.	If your computer doesn't have a USB-A slot or your microcontroller/Arduino board has a different USB connector, then choose an appropriate cable or adapter.

* [SparkFun Brushless Motor Driver - 3 Phase (TMC6300)](https://www.sparkfun.com/products/21867)
* [BLDC Motor](https://www.sparkfun.com/products/20441) (1)
{ .annotate }

	1. This gimbal motor requires a 6 to 8V power supply. However, for zero-load, low-speed testing, we have found that users can get away with utilizing the 5V power from a RedBoard Plus.

* [Power Supply](https://www.sparkfun.com/categories/307 "Click here for a full selection of our available power supplies")
* Soldering Tools (1)
{ .annotate }

	1.	Check out the beginner tool kit below; otherwise, click here for a full selection of our available [soldering tools](https://www.sparkfun.com/categories/49).

* [Headers](https://www.sparkfun.com/categories/381 "Click here for a full selection of our available headers")
* [Small Breadboard](https://www.sparkfun.com/products/12002)
* [Jumper Wires](https://www.sparkfun.com/categories/141 "Click here for a full selection of our wires")

<!-- * [Heat Sink](https://www.sparkfun.com/products/11510 "Thermal tape/compound is NOT included") - Used to help dissipate excess heat
    * [Thermal Tape](https://www.sparkfun.com/products/17054) - To attach a heat sink to the board
	* [Heatsink Compound](https://www.sparkfun.com/products/9599) - To attach a heat sink to the board -->

<table class="pdf">
	<tr>
		<td>
			<a href="https://www.sparkfun.com/products/14743">
				<center>
				USB 3.1 Cable A to C - 3 Foot
				</center>
				<h3 class="title">USB 3.1 Cable A to C - 3 Foot</h3>
			</a>
			CAB-14743
		</td>
		<td>
			<a href="https://www.sparkfun.com/products/18158">
				<center>
				SparkFun RedBoard Plus
				</center>
				<h3 class="title">SparkFun RedBoard Plus</h3>
			</a>
			DEV-18158
		</td>
		<td>
			<a href="https://www.sparkfun.com/products/21867">
				<center>
				Product Thumbnail
				</center>
				<h3 class="title">SparkFun Brushless Motor Driver - 3 Phase (TMC6300)</h3>
			</a>
			ROB-21867
		</td>
		<td>
			<a href="https://www.sparkfun.com/products/12002">
				<center>
				Product Thumbnail
				</center>
				<h3 class="title">Breadboard - Self-Adhesive (White)</h3>
			</a>
			PRT-12002
		</td>
	</tr>
	<tr>
		<td>
			<a href="https://www.sparkfun.com/products/14681">
				<center>
				Product Thumbnail
				</center>
				<h3 class="title">SparkFun Beginner Tool Kit</h3>
			</a>
			TOL-14681
		</td>
		<td>
			<a href="https://www.sparkfun.com/products/116">
				<center>
				Product Thumbnail
				</center>
				<h3 class="title">Break Away Headers - Straight</h3>
			</a>
			PRT-00116
		</td>
		<td>
			<a href="https://www.sparkfun.com/products/8431">
				<center>
				Product Thumbnail
				</center>
				<h3 class="title">Jumper Wires Premium 6" M/M Pack of 10</h3>
			</a>
			PRT-08431
		</td>
		<td>
			<a href="https://www.sparkfun.com/products/9140">
				<center>
				Product Thumbnail
				</center>
				<h3 class="title">Jumper Wires Premium 6" M/F Pack of 10</h3>
			</a>
			PRT-09140
		</td>
	</tr>
	<tr>
		<td>
			<a href="https://www.sparkfun.com/products/20441">
				<center>
				Product Thumbnail
				</center>
				<h3 class="title">Three Phase Brushless Gimbal Stabilizer Motor</h3>
			</a>
			ROB-20441
		</td>
		<td>
			<a href="https://www.sparkfun.com/products/retired/9291">
				<center>
				Product Thumbnail
				</center>
				<h3 class="title">Power Supply - 80W DC Switching Mode</h3>
			</a>
			TOL-09291
	</tr>
</table>

<div class="pdf" markdown>
!!! note "New to soldering?"
	Check out our [Through-Hole Soldering Tutorial](https://learn.sparkfun.com/tutorials/5) for a quick introduction!
	<p align="center">
		<a href="https://learn.sparkfun.com/tutorials/5">How to Solder: Through-Hole Soldering<br>
		Tutorial's thumbnail</a>
	</p>
</div>

<div class="grid cards hide col-4" markdown>

-   <a href="https://www.sparkfun.com/products/14743">**USB 3.1 Cable A to C - 3 Foot**<br>
	CAB-14743

	---

	<figure markdown>
	USB 3.1 Cable A to C - 3 Foot
	</figure></a>

-   <a href="https://www.sparkfun.com/products/18158">**SparkFun RedBoard Plus**<br>
	DEV-18158

	---
	
	<figure markdown>
	SparkFun RedBoard Plus
	</figure></a>

-   <a href="https://www.sparkfun.com/products/21867">
	**Brushless Motor Driver - 3 Phase (TMC6300)**<br>
	ROB-21867

	---

	<figure markdown>
	Product Thumbnail
	</figure></a>

-   <a href="https://www.sparkfun.com/products/12002">
	**Breadboard - Self-Adhesive (White)**<br>
	PRT-12002

	---

	<figure markdown>
	Product Thumbnail
	</figure>
	</a>

-   <a href="https://www.sparkfun.com/products/14681">
	**SparkFun Beginner Tool Kit**<br>
	TOL-14681

	---

	<figure markdown>
	Product Thumbnail
	</figure></a>

	??? note "New to soldering?"
		Check out our [Through-Hole Soldering Tutorial](https://learn.sparkfun.com/tutorials/5) for a quick introduction!
		<p align="center">
			<a href="https://learn.sparkfun.com/tutorials/5">How to Solder: Through-Hole Soldering<br>
			Tutorial's thumbnail</a>
		</p>

-   <a href="https://www.sparkfun.com/products/116">
	**Break Away Headers - Straight**<br>
	PRT-00116

	---

	<figure markdown>
	Product Thumbnail
	</figure>
	</a>

-   <a href="https://www.sparkfun.com/products/8431">
	**Jumper Wires Premium 6" M/M Pack of 10**<br>
	PRT-08431

	---

	<figure markdown>
	Product Thumbnail
	</figure>
	</a>

-   <a href="https://www.sparkfun.com/products/9140">
	**Jumper Wires Premium 6" M/F Pack of 10**<br>
	PRT-09140

	---

	<figure markdown>
	Product Thumbnail
	</figure></a>

-   <a href="https://www.sparkfun.com/products/20441">
	**Three Phase Brushless Gimbal Stabilizer Motor**<br>
	ROB-20441

	---

	<figure markdown>
	Product Thumbnail
	</figure></a>

-   <a href="https://www.sparkfun.com/products/retired/9291">
	**Power Supply - 80W DC Switching Mode**<br>
	TOL-09291

	---

	<figure markdown>
	Product Thumbnail
	</figure></a>

	??? warning "Retired Product"
		Alternatively, a [4xAA battery holder](https://www.sparkfun.com/products/12083) and some [AA batteries](https://www.sparkfun.com/products/15201). However, the maximum current draw will be limited.

-   <a href="https://www.sparkfun.com/products/506">
	**Banana to IC Hook Cables**<br>
	CAB-00506

	---

	<figure markdown>
	Product Thumbnail
	</figure></a>

</div>

??? note "Charge Pump Capacitor"
	The datasheet recommends a 0.1&micro;F capacitor for the charge pump pin, to stabilize the input power supply when there are large swings in the voltage to the motor. Below are links to our 0.1&micro;F capacitors:

	<table class="pdf">
		<tr>
			<td>
				<a href="https://www.sparkfun.com/products/8375">
					<center>
					Product Thumbnail
					</center>
					<h3 class="title">Capacitor Ceramic 0.1uF</h3>
				</a>
				COM-08375
			</td>
			<td>
				<a href="https://www.sparkfun.com/products/13698">
					<center>
					Product Thumbnail
					</center>
					<h3 class="title">SparkFun Capacitor Kit</h3>
				</a>
				KIT-13698
			</td>
		</tr>
	</table>

	<div class="grid cards hide col-4" markdown>

	-   <a href="https://www.sparkfun.com/products/8375">
		**Capacitor Ceramic 0.1uF**<br>
		COM-08375

		---

		<figure markdown>
		Product Thumbnail
		</figure></a>

	-   <a href="https://www.sparkfun.com/products/13698">
		**SparkFun Capacitor Kit**<br>
		KIT-13698

		---

		<figure markdown>
		Product Thumbnail
		</figure></a>

	</div>

??? note "Heat Sink Accessories"
	To attach a heat sink to dissipate excess heat, users will want to check out the following components:

	<table class="pdf">
		<tr>
			<td>
				<a href="https://www.sparkfun.com/products/11510">
					<center>
					Product Thumbnail
					</center>
					<h3 class="title">Small Heatsink</h3>
				</a>
				PRT-11510
			</td>
			<td>
				<a href="https://www.sparkfun.com/products/17054">
					<center>
					Product Thumbnail
					</center>
					<h3 class="title">Thermal Tape 4x4" Square</h3>
				</a>
				PRT-17054
			</td>
			<td>
				<a href="https://www.sparkfun.com/products/9599">
					<center>
					Product Thumbnail
					</center>
					<h3 class="title">Heatsink Compound</h3>
				</a>
				PRT-09599
			</td>
		</tr>
	</table>

	<div class="grid cards hide col-4" markdown>

	-   <a href="https://www.sparkfun.com/products/11510">
		**Small Heatsink**<br>
		PRT-11510

		---

		<figure markdown>
		Product Thumbnail
		</figure></a>

		!!! info "Thermal tape/compound is not included"

	-   <a href="https://www.sparkfun.com/products/17054">
		**Thermal Tape 4x4" Square**<br>
		PRT-17054

		---

		<figure markdown>
		Product Thumbnail
		</figure></a>
	
	-   <a href="https://www.sparkfun.com/products/9599">
		**Heatsink Compound**<br>
		PRT-09599

		---

		<figure markdown>
		Product Thumbnail
		</figure></a>

	</div>

??? note "Current Sensing"
	To perform current sensing from the low-side MOSFETs, users will need to amplify the output signal. Here are some products that users may be interested in:

	<table class="pdf">
		<tr>
			<td>
				<a href="https://www.sparkfun.com/products/14874">
					<center>
					Product Thumbnail
					</center>
					<h3 class="title">SparkFun Configurable OpAmp Board - TSH82</h3>
				</a>
				BOB-14874
			</td>
			<td>
				<a href="https://www.sparkfun.com/products/116">
					<center>
					Product Thumbnail
					</center>
					<h3 class="title">Break Away Headers - Straight</h3>
				</a>
				PRT-00116
			</td>
			<td>
				<a href="https://www.sparkfun.com/products/14681">
					<center>
					Product Thumbnail
					</center>
					<h3 class="title">SparkFun Beginner Tool Kit</h3>
				</a>
				TOL-14681
			</td>
			<td>
				<a href="https://www.sparkfun.com/products/9200">
					<center>
					Product Thumbnail
					</center>
					<h3 class="title">Hobby Knife</h3>
				</a>
				TOL-09200
			</td>
		</tr>
	</table>

	<div class="grid cards hide col-4" markdown>

	-   <a href="https://www.sparkfun.com/products/14874">
		**SparkFun Configurable OpAmp Board - TSH82**<br>
		BOB-14874

		---

		<figure markdown>
		Product Thumbnail
		</figure></a>

		??? tip "New to jumper pads?"
			Check out our [Jumper Pads and PCB Traces Tutorial](https://learn.sparkfun.com/tutorials/664) for a quick introduction!
			<p align="center">
				<a href="https://learn.sparkfun.com/tutorials/664">How to Work with Jumper Pads and PCB Traces<br>
				Tutorial's thumbnail</a>
			</p>
	
	-   <a href="https://www.sparkfun.com/products/116">
		**Break Away Headers - Straight**<br>
		PRT-00116

		---

		<figure markdown>
		Product Thumbnail
		</figure>
		</a>

	-   <a href="https://www.sparkfun.com/products/14681">
		**SparkFun Beginner Tool Kit**<br>
		TOL-14681

		---

		<figure markdown>
		Product Thumbnail
		</figure></a>

		??? note "New to soldering?"
			Check out our [Through-Hole Soldering Tutorial](https://learn.sparkfun.com/tutorials/5) for a quick introduction!
			<p align="center">
				<a href="https://learn.sparkfun.com/tutorials/5">How to Solder: Through-Hole Soldering<br>
				Tutorial's thumbnail</a>
			</p>
	
	-  <a href="https://www.sparkfun.com/products/9200">
		**Hobby Knife**<br>
		TOL-09200

		---

		<figure markdown>
		Product Thumbnail
		</figure>
		</a>

	</div>

??? note "Jumper Modification"
	To modify the [jumper](hardware_overview/#jumper), users will need [soldering equipment](https://www.sparkfun.com/categories/49) and/or a [hobby knife](https://www.sparkfun.com/categories/379).

	!!! tip "New to jumper pads?"
		Check out our [Jumper Pads and PCB Traces Tutorial](https://learn.sparkfun.com/tutorials/664) for a quick introduction!
		<p align="center">
			<a href="https://learn.sparkfun.com/tutorials/664">How to Work with Jumper Pads and PCB Traces<br>
			Tutorial's thumbnail</a>
		</p>

	<table class="pdf">
		<tr>
			<td>
				<a href="https://www.sparkfun.com/products/9325">
					<center>
					Product Thumbnail
					</center>
					<h3 class="title">Solder Lead Free - 100-gram Spool</h3>
				</a>
				TOL-09325
			</td>
			<td>
				<a href="https://www.sparkfun.com/products/14228">
					<center>
					Product Thumbnail
					</center>
					<h3 class="title">Weller WLC100 Soldering Station</h3>
				</a>
				TOL-14228
			</td>
			<td>
				<a href="https://www.sparkfun.com/products/14579">
					<center>
					Product Thumbnail
					</center>
					<h3 class="title">Chip Quik No-Clean Flux Pen - 10mL</h3>
				</a>
				TOL-14579
			</td>
			<td>
				<a href="https://www.sparkfun.com/products/9200">
					<center>
					Product Thumbnail
					</center>
					<h3 class="title">Hobby Knife</h3>
				</a>
				TOL-09200
			</td>
		</tr>
	</table>

	<div class="grid cards hide col-4" markdown>

	-   <a href="https://www.sparkfun.com/products/9325">
		**Solder Lead Free - 100-gram Spool**<br>
		TOL-09325

		---

		<figure markdown>
		Product Thumbnail
		</figure></a>

	-   <a href="https://www.sparkfun.com/products/14228">**Weller WLC100 Soldering Station**<br>
		TOL-14228

		---
		
		<figure markdown>
		Product Thumbnail
		</figure></a>

	-   <a href="https://www.sparkfun.com/products/14579">
		**Chip Quik No-Clean Flux Pen - 10mL**<br>
		TOL-14579

		---

		<figure markdown>
		Product Thumbnail
		</figure></a>

	-   <a href="https://www.sparkfun.com/products/9200">
		**Hobby Knife**<br>
		TOL-09200

		---

		<figure markdown>
		Product Thumbnail
		</figure>
		</a>
	</div>

??? note "Alternative Motor Connections"
	For users with less precise soldering skills, we recommend these wiring options as they are less dependent on hoe the leads to the motor are tinned. Additionally, user may find the alligator clips useful for motors with thicker wires.

	<table class="pdf">
		<tr>
			<td>
				<a href="https://www.sparkfun.com/products/9741">
					<center>
					Product Thumbnail
					</center>
					<h3 class="title">IC Hook with Pigtail</h3>
				</a>
				CAB-09741
			</td>
			<td>
				<a href="https://www.sparkfun.com/products/13191">
					<center>
					Product Thumbnail
					</center>
					<h3 class="title">Alligator Clip with Pigtail (4 Pack)</h3>
				</a>
				CAB-13191
			</td>
		</tr>
	</table>

	<div class="grid cards hide col-4" markdown>

	-   <a href="https://www.sparkfun.com/products/9741">
		**IC Hook with Pigtail**<br>
		CAB-09741

		---

		<figure markdown>
		Product Thumbnail
		</figure></a>

	-   <a href="https://www.sparkfun.com/products/13191">
		**Alligator Clip with Pigtail (4 Pack)**<br>
		CAB-13191

		---

		<figure markdown>
		Product Thumbnail
		</figure>
		</a>

	</div>

??? note "Alternative Power Source"
	Here are alternative battery options to power the TMC6300 motor driver. These batteries should be in the operation voltage range for the gimbal motor (just set the max charge to 8V). Additionally, they are capable of supplying more than the maximum current draw of the TMC6300.

	<table class="pdf">
		<tr>
			<td>
				<a href="https://www.sparkfun.com/products/16793">
					<center>
					Product Thumbnail
					</center>
					<h3 class="title">SkyRC IMAX B6 V2 Professional Balance Charger / Discharger</h3>
				</a>
				PRT-16793
			</td>
			<td>
				<a href="https://www.sparkfun.com/products/11856">
					<center>
					Product Thumbnail
					</center>
					<h3 class="title">Lithium Ion Battery - 2200mAh 7.4v</h3>
				</a>
				PRT-11856
			</td>
			<td>
				<a href="https://www.sparkfun.com/products/11855">
					<center>
					Product Thumbnail
					</center>
					<h3 class="title">Lithium Ion Battery - 1000mAh 7.4v</h3>
				</a>
				PRT-11855
			</td>
		</tr>
	</table>

	<div class="grid cards hide col-4" markdown>

	-   <a href="https://www.sparkfun.com/products/16793">
		**SkyRC IMAX B6 V2 Professional Balance Charger / Discharger**<br>
		PRT-16793

		---

		<figure markdown>
		Product Thumbnail
		</figure></a>

	-   <a href="https://www.sparkfun.com/products/11856">
		**Lithium Ion Battery - 2200mAh 7.4v**<br>
		PRT-11856

		---

		<figure markdown>
		Product Thumbnail
		</figure></a>
	
	-   <a href="https://www.sparkfun.com/products/11855">
		**Lithium Ion Battery - 1000mAh 7.4v**<br>
		PRT-11855

		---

		<figure markdown>
		Product Thumbnail
		</figure></a>

	</div>

??? note "DC Motor Example"
	For users who wish to try out the H-bridge/DC motor example, they will also need a DC motor:

	<div class="grid cards col-4" markdown>

	-   <a href="https://www.sparkfun.com/products/21245">
		**Hobby Gearmotor - 140 RPM**<br>
		ROB-21245

		---

		<figure markdown>
		Product Thumbnail
		</figure></a>

	</div>

## :material-bookshelf:&nbsp;Suggested Reading

As a more sophisticated product, we will skip over the more fundamental tutorials (i.e. [**Ohm's Law**](https://learn.sparkfun.com/tutorials/voltage-current-resistance-and-ohms-law) and [**What is Electricity?**](https://learn.sparkfun.com/tutorials/what-is-electricity)). However, below are a few tutorials that may help users familiarize themselves with various aspects of the board.

<table class="pdf">
	<tr>
		<td align="center">
			<a href="https://learn.sparkfun.com/tutorials/72">Electric Power<br>
			Tutorial Thumbnail</a>
		</td>
		<td align="center">
			<a href="https://learn.sparkfun.com/tutorials/18">Connector Basics<br>
			Tutorial Thumbnail</a>
		</td>
        <td align="center">
			<a href="https://learn.sparkfun.com/tutorials/41">Working with Wire<br>
			Tutorial Thumbnail</a>
		</td>
		<td align="center">
			<a href="https://learn.sparkfun.com/tutorials/36">How to Power a Project<br>
			Tutorial Thumbnail</a>
		</td>
    </tr>
	<tr>
		<td align="center">
			<a href="https://learn.sparkfun.com/tutorials/26">What is a Circuit?<br>
			Tutorial Thumbnail</a>
		</td>
		<td align="center">
			<a href="https://learn.sparkfun.com/tutorials/115">Alternating Current (AC) vs. Direct Current (DC)<br>
			Tutorial Thumbnail</a>
		</td>
        <td align="center">
			<a href="https://learn.sparkfun.com/tutorials/75">Polarity<br>
			Tutorial Thumbnail</a>
		</td>
		<td align="center">
			<a href="https://learn.sparkfun.com/tutorials/62">Logic Levels<br>
			Tutorial Thumbnail</a>
		</td>
	</tr>
    <tr>
		<td align="center">
			<a href="https://learn.sparkfun.com/tutorials/126">Installing the Arduino IDE<br>
			Tutorial Thumbnail</a>
		</td>
		<td align="center">
			<a href="https://learn.sparkfun.com/tutorials/51">Installing an Arduino Library<br>
			Tutorial Thumbnail</a>
		</td>
		<td align="center">
			<a href="https://learn.sparkfun.com/tutorials/194">How to Solder: Through-Hole Soldering<br>
			Tutorial Thumbnail</a>
		</td>
		<td align="center">
			<a href="https://learn.sparkfun.com/tutorials/8">How to Work with Jumper Pads and PCB Traces<br>
			Tutorial Thumbnail</a>
		</td>
	</tr>
	    <tr>
		<td align="center">
			<a href="https://learn.sparkfun.com/tutorials/61">Motors and Selecting the Right One<br>
			Tutorial Thumbnail</a>
		</td>
		<td align="center">
			<a href="https://learn.sparkfun.com/tutorials/15">Pulse Width Modulation<br>
			Tutorial Thumbnail</a>
		</td>
		<td align="center">
			<a href="https://learn.sparkfun.com/tutorials/5">How to Use an Oscilloscope<br>
			Tutorial Thumbnail</a>
		</td>
		<td align="center">
			<a href="https://learn.sparkfun.com/tutorials/664">Serial Communication<br>
			Tutorial Thumbnail</a>
		</td>
	</tr>
</table>

<div class="grid cards hide col-4" markdown align="center">

-   <a href="https://learn.sparkfun.com/tutorials/72">
	**Electric Power**

	---
	
	<figure markdown>
	Tutorial Thumbnail
	</figure></a>

-   <a href="https://learn.sparkfun.com/tutorials/18">
	**Connector Basics**

	---
	
	<figure markdown>
	Tutorial Thumbnail
	</figure></a>

-   <a href="https://learn.sparkfun.com/tutorials/41">
	**Working with Wire**

	---
	
	<figure markdown>
	Tutorial Thumbnail
	</figure></a>

-   <a href="https://learn.sparkfun.com/tutorials/36">
	**How to Power a Project**

	---
	
	<figure markdown>
	Tutorial Thumbnail
	</figure></a>

-   <a href="https://learn.sparkfun.com/tutorials/26">
	**What is a Circuit?**

	---
	
	<figure markdown>
	Tutorial Thumbnail
	</figure></a>

-   <a href="https://learn.sparkfun.com/tutorials/115">
	**Alternating Current (AC) vs. Direct Current (DC)**

	---
	
	<figure markdown>
	Tutorial Thumbnail
	</figure></a>

-   <a href="https://learn.sparkfun.com/tutorials/75">
	**Polarity**

	---
	
	<figure markdown>
	Tutorial Thumbnail
	</figure></a>

-   <a href="https://learn.sparkfun.com/tutorials/62">
	**Logic Levels**

	---
	
	<figure markdown>
	Tutorial Thumbnail
	</figure></a>

-   <a href="https://learn.sparkfun.com/tutorials/61">**Installing the Arduino IDE**

	---
	
	<figure markdown>
	Tutorial Thumbnail
	</figure></a>

-   <a href="https://learn.sparkfun.com/tutorials/15">**Installing an Arduino Library**

	---
	
	<figure markdown>
	Tutorial Thumbnail
	</figure></a>

-   <a href="https://learn.sparkfun.com/tutorials/5">
	**How to Solder: Through-Hole Soldering**

	---
	
	<figure markdown>
	Tutorial Thumbnail
	</figure></a>

-   <a href="https://learn.sparkfun.com/tutorials/664">
	**How to Work with Jumper Pads and PCB Traces**

	---
	
	<figure markdown>
	Tutorial Thumbnail
	</figure></a>

-   <a href="https://learn.sparkfun.com/tutorials/126">
	**Motors and Selecting the Right One**

	---
	
	<figure markdown>
	Tutorial Thumbnail
	</figure></a>

-   <a href="https://learn.sparkfun.com/tutorials/51">
	**Pulse Width Modulation**

	---
	
	<figure markdown>
	Tutorial Thumbnail
	</figure></a>

-   <a href="https://learn.sparkfun.com/tutorials/194">
	**How to Use an Oscilloscope**

	---
	
	<figure markdown>
	Tutorial Thumbnail
	</figure></a>

-   <a href="https://learn.sparkfun.com/tutorials/8">
	**Serial Communication**

	---
	
	<figure markdown>
	Tutorial Thumbnail
	</figure></a>

</div>

??? info "Need to control a different type of motor?"
	This tutorial is primarily focused on utilizing the TMC6300 motor driver to control a 3-phase brushless DC (BLDC) motor. While the versatility of this chipset allows for the control of other motor types, we would recommend less experienced users to explore products designed for those specific motors or actuators. Below, are additional product tutorials and resources for our other actuator and motor types:

	=== "Brushed DC Motors"

		<div class="grid cards col-4" markdown align="center">

		-   <a href="https://learn.sparkfun.com/tutorials/934">
			**Hookup Guide for the Qwiic Motor Driver**

			---
			
			<figure markdown>
			Tutorial Thumbnail
			</figure></a>

		-   <a href="https://learn.sparkfun.com/tutorials/526">
			**TB6612FNG Hookup Guide**

			---
			
			<figure markdown>
			Tutorial Thumbnail
			</figure></a>
		
		</div>

	=== "Stepper Motors"

		<div class="grid cards col-4" markdown align="center">

		-   <a href="https://learn.sparkfun.com/tutorials/1200">
			**SparkFun ProDriver Hookup Guide**

			---
			
			<figure markdown>
			Tutorial Thumbnail
			</figure></a>

		-   <a href="https://learn.sparkfun.com/tutorials/210">
			**Easy Driver Hook-up Guide**

			---
			
			<figure markdown>
			Tutorial Thumbnail
			</figure></a>
		
		</div>

	=== "Servos"

		<div class="grid cards col-4" markdown align="center">

		-   <a href="https://learn.sparkfun.com/tutorials/1109">
			**Basic Servo Control for Beginners**

			---
			
			<figure markdown>
			Tutorial Thumbnail
			</figure></a>

		-   <a href="https://learn.sparkfun.com/tutorials/526">
			**Hobby Servo Tutorial**

			---
			
			<figure markdown>
			Tutorial Thumbnail
			</figure></a>
		
		-   <a href="https://learn.sparkfun.com/tutorials/910">
			**Pi Servo pHAT (v2) Hookup Guide**

			---
			
			<figure markdown>
			Tutorial Thumbnail
			</figure></a>
		
		</div>

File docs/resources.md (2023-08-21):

## Product Resources

* :sfe-logo: [Product Page](https://www.sparkfun.com/products/21867)
* Component Documentation
    * :fontawesome-solid-file-pdf: [TMC6300 Datasheet](./component_documentation/TMC6300.pdf)
* :material-folder-cog: Design Files:
    * :fontawesome-solid-file-pdf: [Board Dimensions](./board_files/dimensions.pdf)
    * :fontawesome-solid-file-pdf: [Schematic](./board_files/schematic.pdf)
    * :material-folder-zip: [Eagle Files](./board_files/eagle_files.zip)
* Arduino Library:
    * :material-github: [Simple FOC](https://github.com/simplefoc/Arduino-FOC)
    * :material-file-document-multiple: [Documentation](https://docs.simplefoc.com/)
        * [Installation](https://docs.simplefoc.com/library_download)
        * [Supported Hardware](https://docs.simplefoc.com/supported_hardware)
        * [Code Overview](https://docs.simplefoc.com/code)
* :material-youtube: [SFE Product Showcase](https://youtu.be/I0sJSTlUF_E)
* :material-github: [Hardware Repo](https://github.com/sparkfun/SparkFun_Three_Phase_Motor_Driver-TMC6300)

### Additional Resources

* [Motors and Motor Driver Product Category](https://www.sparkfun.com/categories/178)
* :material-account-supervisor: [SparkFun Technical Assistance](https://www.sparkfun.com/technical_assistance)

## 🏭&nbsp;Manufacturer's Resources
Analog Devices + Trinamic also provides great resources for the TMC6300 motor driver:

* [TMC6300 Product Page](https://www.trinamic.com/products/integrated-circuits/details/tmc6300-la/)
    * [Block Diagram/Pinout](https://www.trinamic.com/products/integrated-circuits/details/tmc6300-la/#block-diagram)
    * :material-file-document: [Datasheet](https://www.trinamic.com/products/integrated-circuits/details/tmc6300-la/#downloads-2)
    * :material-file-document-multiple: [Application Notes](https://www.trinamic.com/products/integrated-circuits/details/tmc6300-la/#downloads-1)
* :material-youtube: [Trinamic: TMC6300 Product Training Module](https://youtu.be/WCvQjW1gSNY)
* :material-head-question: [Technical Support Page](https://www.trinamic.com/support/technical-support/)

<center>
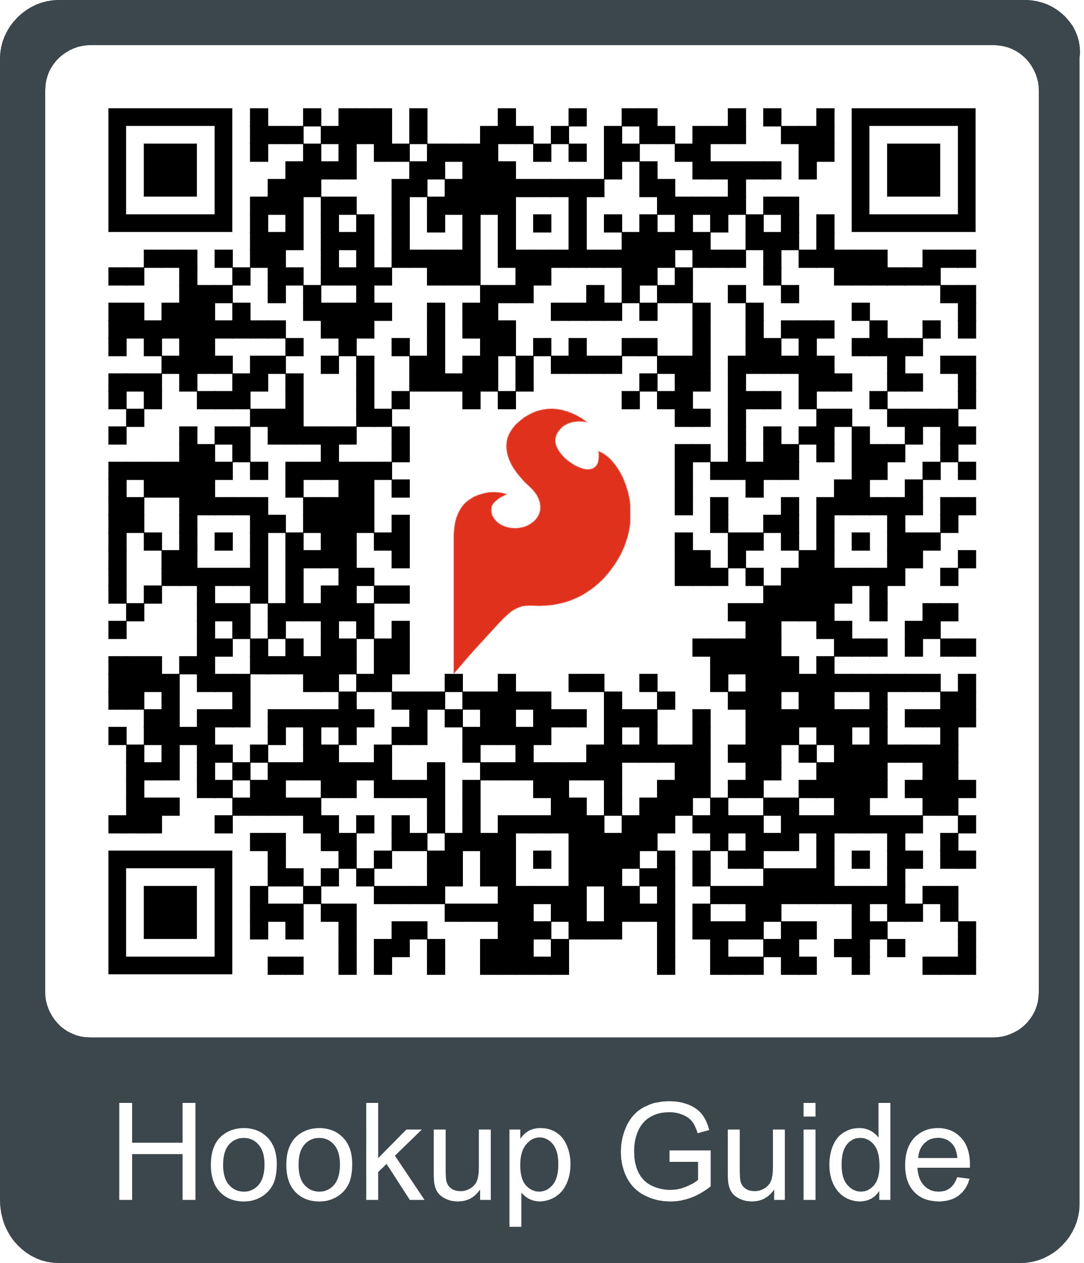
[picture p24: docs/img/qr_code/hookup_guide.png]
QR code to the hookup guide

</center>

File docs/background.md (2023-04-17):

---
icon: material/bookshelf
---

Below, are several articles, application notes, and other technical resources on 3-phase motors and utilizing a field oriented control (FOC) scheme:

* Microchip Technology
    * [AN885: Brushless DC (BLDC) Motor Fundamentals](https://ww1.microchip.com/downloads/en/appnotes/00885a.pdf)
    * [AN2757: Sensored (Encoder-Based) Field Oriented Control of Three-Phase Permanent Magnet Synchronous Motor (PMSM)](https://ww1.microchip.com/downloads/en/Appnotes/Sensored-Encoder-Based%29-Field-Oriented-Control-of-Three-Phase-%20Permanent-%20Magnet-%20Synchronous-DS00002757A.pdf)
    * [AN1078: Sensorless Field Oriented Control of a PMSM](https://www.eeweb.com/wp-content/uploads/articles-app-notes-files-sensorless-field-oriented-control-of-a-pmsm-1340055193.pdf)
    * [AVR32723: Sensor Field Oriented Control for Brushless DC motors with AT32UC3B0256](https://ww1.microchip.com/downloads/en/Appnotes/doc32126.pdf)
* Diodes Incorporated
    * [AN1164: Introduction to Brushless DC Motors](https://www.diodes.com/assets/Uploads/AN1164-BLDC-Motors.pdf)
* Monolithic Power Systems
    * [AN047: Brushless DC Motor Fundamentals](https://www.monolithicpower.com/media/document/Brushless_DC_Motor_Fundamentals.pdf)
* Texas Instruments
    * [Demystifying BLDC motor commutation: Trap, Sine, & FOC](https://www.ti.com/lit/ml/slyp711/slyp711.pdf)
    * [Sensored Field Oriented Control of 3-Phase Permanent Magnet Synchronous Motors](https://www.ti.com/lit/an/sprabq2/sprabq2.pdf)
    * [Sensorless Field Oriented Control of 3-Phase Permanent Magnet Synchronous Motors](https://www.ti.com/lit/an/sprabq3/sprabq3.pdf)
    * [Brushless-DC Motor Driver Considerations and Selection Guide](https://www.ti.com/lit/an/slvaes1a/slvaes1a.pdf)
    * [High Performance Brushless DC Motor Control](https://www.ti.com/lit/an/sprt703/sprt703.pdf)
    * :material-video-box:&nbsp;[Field oriented control of permanent magnet synchronous motors](https://www.ti.com/video/3881563245001)
    * :material-video-box:&nbsp;[Field Oriented Control of Permanent Magnet Motors](https://www.ti.com/video/3871706529001)
        * :material-youtube:&nbsp;[Field Oriented Control of Permanent Magnet Motors](https://www.youtube.com/watch?v=cdiZUszYLiA)
* MATLAB
    * :material-youtube:&nbsp;[Motor Control, Part 4: Understanding Field-Oriented Control](https://youtu.be/YPD1_rcXBIE)
* Analog Devices + Trinamic
    * [FOC As Hardware Building Block](https://www.trinamic.com/technology/motor-control-technology/field-oriented-control/)
* Infineon Technologies
    * [Motor Handbook](https://www.infineon.com/dgdl/Infineon-motorcontrol_handbook-AdditionalTechnicalInformation-v01_00-EN.pdf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)
    * [AN204469 - FM3 Family 3-Phase PMSM FOC Control](https://www.infineon.com/dgdl/Infineon-AN204469_FM3_Family_3_Phase_PMSM_FOC_Control-ApplicationNotes-v03_00-EN.pdf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)
    * [Block commutation vs. FOC in power tool motor control](https://www.infineon.com/dgdl/Infineon-Motor_power_tool_Block_Commutation_vs_FOC-ApplicationNotes-v01_00-EN.pdf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)
    * :material-presentation-play:&nbsp;[Motor control for BLDC: block commutation vs. field-oriented control](https://www.infineon.com/cms/media/eLearning/PSS/PSS_eLearning_Motor_control_for_BLDC_in_low_voltage_drives_english/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)
* ST Microelectronics
    * [AN5397: Current Sensing in Motion Control Applications](https://www.st.com/resource/en/application_note/an5397-current-sensing-in-motion-control-applications-stmicroelectronics.pdf)
    * [AN4220: Sensorless Six-Step BLDC Commutation](https://www.st.com/resource/en/application_note/an4220-sensorless-sixstep-bldc-commutation-stmicroelectronics.pdf)

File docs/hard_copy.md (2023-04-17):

---
icon: material/book-open-variant
---

Need to download or print our hookup guide?

* [Print :fontawesome-solid-print:](../single_page) (Single-Page View)
    * To save as a `*.pdf` file, select the **Printer** or **Destination** labeled ++"Save as PDF"++. *(Instructions will vary based on the browser)*
* [Download :fontawesome-regular-file-pdf:](../board_files/hookup_guide.pdf) *(Beta - demonstration only)*

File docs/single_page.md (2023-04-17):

---
hide:
  - navigation
  - toc
icon: fontawesome/solid/scroll
---

--8<-- "./docs/getting_started.md:5"

# Hardware Overview
--8<-- "./docs/hardware_overview.md:5"

# Hardware Assembly
--8<-- "./docs/component_assembly.md:5"
--8<-- "./docs/hardware_assembly.md:5"

# Software Overview
--8<-- "./docs/software_overview.md:5"

## BLDC Example
--8<-- "./docs/arduino_examples/example-BLDC.md"

## DC Motor Example
--8<-- "./docs/arduino_examples/example-DC.md"

# Troubleshooting Tips
--8<-- "./docs/troubleshooting_tips.md:5"

# Resources:
--8<-- "./docs/resources.md"

## Background Resources
--8<-- "./docs/background.md:5"

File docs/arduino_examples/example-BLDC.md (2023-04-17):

## Hardware Assembly

Users should already have followed the instructions from the [component assembly](../../component_assembly) and [example setups](../../hardware_assembly) sections to setup their hardware for this example.

<figure markdown>

<figcaption markdown>
A graphical representation of the connections between the [RedBoard Plus](https://www.sparkfun.com/products/18158) and a [breadboard](https://www.sparkfun.com/products/12002) with the [TMC6300 motor driver](https://www.sparkfun.com/products/21867) attached.
</figcaption>
</figure>

### RedBoard Plus to TMC6300

Connect the following pins from the RedBoard Plus to the TMC6300.

--8<-- "./docs/hardware_assembly.md:12:26"

### Connecting the Gimbal Motor

--8<-- "./docs/hardware_assembly.md:45:52"

### Powering the TMC6300

If users are unable to find a suitable power source, we have found that the 5V power output from the RedBoard Plus is sufficient to drive the gimbal motor, under a no load condition at low speeds.

--8<-- "./docs/hardware_assembly.md:83:97"

## Example Code

After installing and setting up the Arduino IDE and the Simple FOC Arduino library, users will need to upload the following example code to the RedBoard Plus. This code can be copied or downloaded below:

<center>
[:octicons-download-16:{ .heart } Download `BLDC.ino` Example Code](../BLDC/BLDC.ino){ .md-button .md-button--primary }
</center>

!!! code "Example Code"
    ``` c++ title="BLDC.ino"
        --8<-- "./docs/arduino_examples/BLDC/BLDC.ino"
    ```

### Running the Motor

Be default, the motor should spin automatically. However, if users wish to control the speed of the motor, they can uncomment lines **21-22** and **56-57** of code and reprogram the RedBoard Plus.

??? code "Code Changes Highlighted"
    Uncomment the following lines of code (**21-22** and **56-57**):

    ``` c++ hl_lines="21-22 56-57" title="BLDC.ino"
        --8<-- "./docs/arduino_examples/BLDC/BLDC.ino"
    ```

In order to drive the motor, users will need to access the [serial monitor](https://learn.sparkfun.com/tutorials/8) and provide the [commands](https://docs.simplefoc.com/commands_source) necessary to drive the motor. A full list of the available commands can be found in the [Simple FOC Arduino library documentation](https://docs.simplefoc.com/commands_source). However, only the `T` and `L` commands are enabled in the example code.

* Sending a `T` command will set the target motor velocity in rads/s
    * Example - Entering `T6` into the serial monitor, will set the target motor velocity to 6 radians/s.
* Sending a `L` command will set the voltage limit of the motor driver and in turn, the current limit *(voltage_limit / motor_resistance)*
    * Example - Entering `L5` into the serial monitor, will set the voltage limit to 5V and the current limit to .5A *(5V/10&ohm;)*.

!!! tip "Baud Rate"
    THe serial monitor baud rate should be configured to 115200bps.

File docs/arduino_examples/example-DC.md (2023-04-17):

## Hardware Assembly

Users should already have followed the instructions from the [component assembly](../../component_assembly) and [example setups](../../hardware_assembly) sections to setup their hardware for this example.

<figure markdown>

<figcaption markdown>
A graphical representation of the connections between the [RedBoard Plus](https://www.sparkfun.com/products/18158) and a [breadboard](https://www.sparkfun.com/products/12002) with the [TMC6300 motor driver](https://www.sparkfun.com/products/21867) attached.
</figcaption>
</figure>

### RedBoard Plus to TMC6300

Connect the following pins from the RedBoard Plus to the TMC6300.

--8<-- "./docs/hardware_assembly.md:12:26"

### Connecting the DC Motor

--8<-- "./docs/hardware_assembly.md:71:71"

### Powering the TMC6300

If users are unable to find a suitable power source, we have found that the 5V power output from the RedBoard Plus is sufficient to drive the gimbal motor, under a no load condition at low speeds.

--8<-- "./docs/hardware_assembly.md:83:97"

## Example Code

After installing and setting up the Arduino IDE and the Simple FOC Arduino library, users will need to upload the following example code to the RedBoard Plus. This code can be copied or downloaded below:

<center>
[:octicons-download-16:{ .heart } Download `DC.ino` Example Code](../DC/DC.ino){ .md-button .md-button--primary }
</center>

!!! code "Example Code"
    ``` c++ title="DC.ino"
        --8<-- "./docs/arduino_examples/DC/DC.ino"
    ```

### Running the Motor

Be default, the motor should spin automatically. However, if users wish to control the motor, they can modify lines **30** and **33** of code and reprogram the RedBoard Plus. These lines control the high and low-side MOSFETS of the H-bridge directly through pins `5`, `6`, `9`, and `10`.

??? code "Code Changes Highlighted"
    MOdify the following lines of code (**30** and **33**):

    ``` c++ hl_lines="30 33" title="DC.ino"
        --8<-- "./docs/arduino_examples/DC/DC.ino"
    ```

* The PWM voltage value `driver.setPwm(voltage_value,0,0)` affects the speed of the motor.
* The position of this value inr elation to the PWM drive channel `driver.setPwm(channel_v,channel_w,0)` affects the direction.

??? tip
    Users may also be interested in the [SimpleDC Motor library](https://docs.simplefoc.com/dc_motors_library) to drive DC motors with the Simple FOC Arduino library.

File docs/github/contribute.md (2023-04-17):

# Contribute: Make an Augmentation!
Spot an improvement opportunity? Feel free to contribute to our open-source design and documentation. 

## :material-file-document-multiple:&nbsp;Improve our Documentation
All of this documentation can be modified by you! Please help us make it better.

* These pages are contained in the [`docs` folder](https://github.com/sparkfun/SparkFun_Three_Phase_Motor_Driver-TMC6300/tree/main/docs) of the [SparkFun TMC6300 motor driver repository](https://github.com/sparkfun/SparkFun_Three_Phase_Motor_Driver-TMC6300).

<!-- ### :material-source-pull:&nbsp;Submit a Correction -->
### Submit a Correction

1. With a GitHub account, [fork this repository](https://github.com/sparkfun/SparkFun_Three_Phase_Motor_Driver-TMC6300/fork).
2. Add your corrections or improvements to the markdown file.
3. File a pull request with your changes, and enjoy making the ~~words~~ ~~worlds~~ world a better place.
	* Once received, the documentation specialist will automatically be notified.
	* We will review your suggested improvements to make sure they are correct and fit within our documentation standards.

## :material-cog:&nbsp;Improve our Hardware Design
All of our designs are open-source! Please help us make it better.

* Our board design files are contained in the [`Hardware` folder](https://github.com/sparkfun/SparkFun_Three_Phase_Motor_Driver-TMC6300/tree/main/Hardware) of the [SparkFun TMC6300 motor driver repository](https://github.com/sparkfun/SparkFun_Three_Phase_Motor_Driver-TMC6300).

<!-- ### :material-source-pull:&nbsp;Submit a Design Enhancement -->
### Submit a Design Enhancement

1. With a GitHub account, [fork this repository](https://github.com/sparkfun/SparkFun_Three_Phase_Motor_Driver-TMC6300/fork).
2. Add your design augmentation(s)
3. File a pull request with your changes, and enjoy making the ~~words~~ ~~worlds~~ world a better place.
	1. Once received, the engineer in charge of the original design will automatically be notified.
	2. We will review your suggested improvement(s) to verify that they are within our board design standards and meet our product design requirements.
	3. If approved, we will flag these changes for our next board revision. Congrats! 🍻

		!!! info
			Even if your suggestion is accepted, these changes may not be immediately available for purchase. We may have to cycle through our current product inventory first.

## Contributors&nbsp;:clap:
Let's provide some recognition to the contributors for this project!

GitHub Contributors Image
<br>


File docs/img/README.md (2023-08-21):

img directory
====================
This folder should contain the images for the product documentation

## General Images
* `sfe_logo_sm.png` - SparkFun flame logo (Cover page for with-pdf extension)
* `sfe_logo_sq.png` - SparkFun flame logo (favicon)

## Directory
* `hookup_guide` - Images for the hookup guide pages

## QR Codes
* [QR code generator](https://qrgenerator.org/)
    * Flame Color: #E0311D
    * Frame Color: #3C464D
* [Remove meta data from svg](https://jakearchibald.github.io/svgomg/)

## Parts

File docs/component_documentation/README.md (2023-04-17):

component_documentation directory
====================

A copy of the datasheets, user manuals, programming guides, etc. of the major electrical components on the board.

* [TMC6300 Datasheet](TMC6300.pdf) (PDF)

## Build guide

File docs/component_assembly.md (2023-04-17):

---
icon: material/tools
---

## TMC6300 Motor Driver

### :material-soldering-iron:&nbsp;Headers

??? note "New to soldering?"
	If you have never soldered before or need a quick refresher, check out our [How to Solder: Through-Hole Soldering](https://learn.sparkfun.com/tutorials/how-to-solder-through-hole-soldering) guide.
	<p align="center">
		<a href="https://learn.sparkfun.com/tutorials/5">How to Solder: Through-Hole Soldering<br>
		Tutorial's thumbnail</a>
	</p>

The pins on the SparkFun TMC6300 motor driver are broken out to 0.1"-spaced pins on the outer edges of the board. When selecting headers, be sure you are aware of the functionality and board orientation required.

<figure markdown>
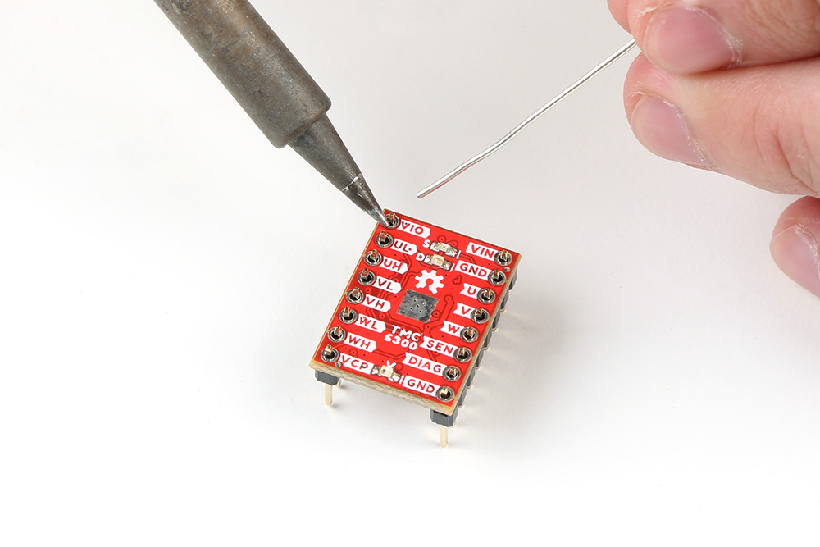
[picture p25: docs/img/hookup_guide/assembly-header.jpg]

<figcaption markdown>
Soldering headers to the TMC6300 motor driver.
</figcaption>
</figure>

!!! tip
	Please be aware that the side of the board with the silkscreen labeld for the pins and the heat sink pad is, technically the top side of the board when in use.

	<div class="grid cards" markdown>

	-	<figure markdown>
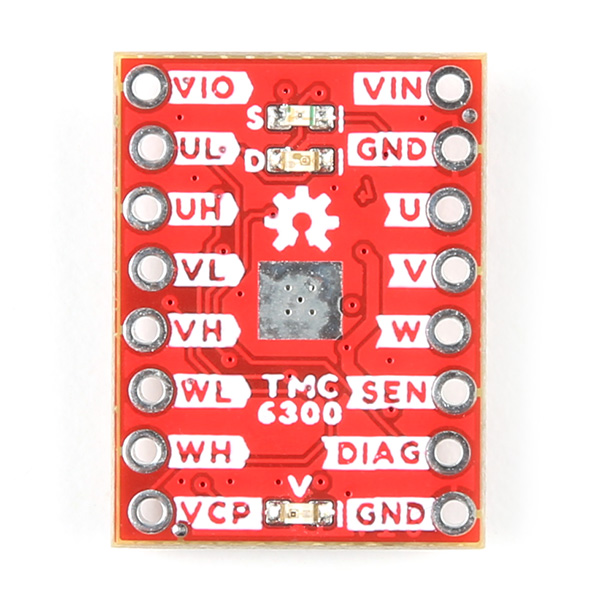
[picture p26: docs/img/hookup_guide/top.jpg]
		
		<figcaption markdown>
		Top side of the TMC6300 motor driver.
		</figcaption>
		</figure>

	-	<figure markdown>
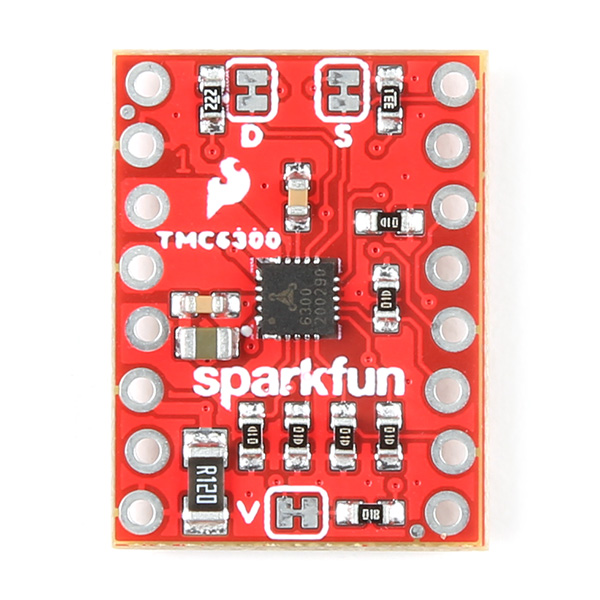
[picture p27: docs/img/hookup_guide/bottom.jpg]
		
		<figcaption markdown>
		Bottom side of the TMC6300 motor driver.
		</figcaption>
		</figure>

	</div>

!!! info "Staggered PTH Pins"
	The pins on the board may appear to be offset or crooked; this is by design, we stagger the holes along a specific center alignment. This reduces the geometric tolerance between the holes and header pins along a single axis, which helps to hold the header in place and keeps the pins more orthogonal to the board when soldering.

### Heat Sink

!!! tip
    With larger heat sinks, we recommend a test fit and attaching it last to avoid conflicts with other parts of the board. For example, the heat sink could block the PTH pins/slots or access to the jumper pad.

	!!! warning "Copper Heat Sink"
		Users may be tempted to use our [copper heatsink](https://www.sparkfun.com/products/18704) on their board. However, we highly advise against using the copper heat sink because it barely fits and will likely cause a short across one of the pins.

		<div class="grid cards hide" markdown>

		-   <figure markdown>
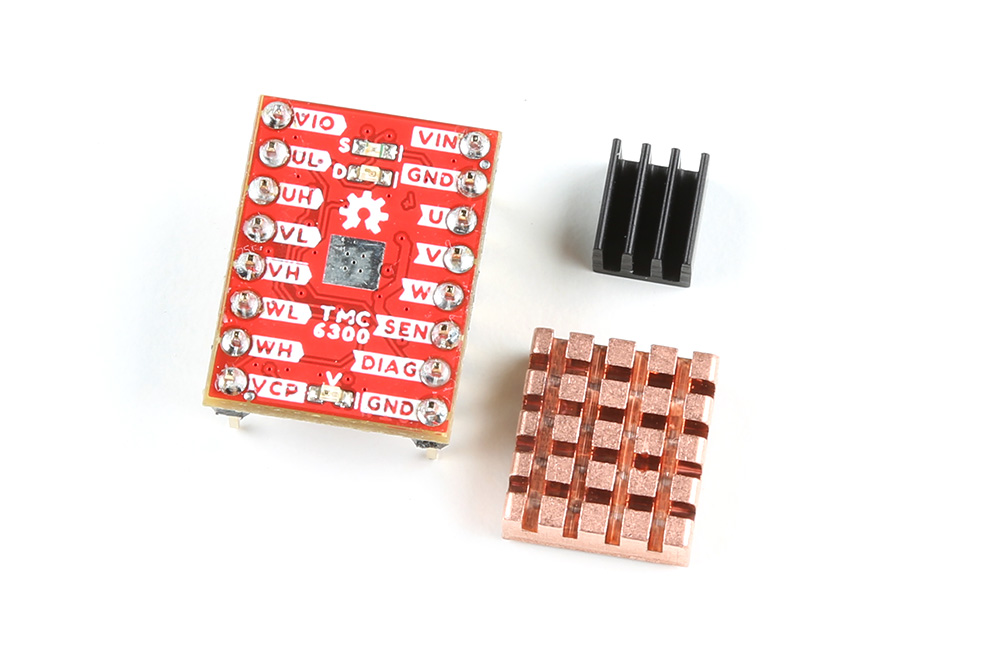
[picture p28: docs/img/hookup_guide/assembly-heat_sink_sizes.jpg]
			
			<figcaption markdown>
			Different [heat sinks](https://www.sparkfun.com/categories/tags/heatsink) next to the TMC6300 motor driver.
			</figcaption>
			</figure>

		-   <figure markdown>
			
			<figcaption markdown>
			Copper heat sink not fitting on the TMC6300 motor driver.
			</figcaption>
			</figure>
		
		</div>

		<center>
		<table class="pdf">
			<tr>
				<td align="center">
					<br>
					<i>Different <a href="https://www.sparkfun.com/categories/tags/heatsink">heat sinks</a> next to the TMC6300 motor driver.</i>
				</td>
				<td align="center">
					<br>
					<i>Copper heat sink not fitting on the TMC6300 motor driver.</i>
				</td>
			</tr>
		</table>
		</center>

To attach a [heat sink](https://www.sparkfun.com/products/11510) to the board, users will also need a piece of [thermal tape](https://www.sparkfun.com/products/17054). We recommend the following procedure:

1. Cut out a piece of [thermal tape](https://www.sparkfun.com/products/17054) to fit the bottom of the [heat sink](https://www.sparkfun.com/products/11510).
	
	!!! tip
		Covering the entire bottom of the heat sink can insulate the electrical contacts on the board from shorting.

    * For a perfect fit, users can place the heat sink over the tape and trace the outline to cut with scissors.
    * For a perfect fit, users can also place the heat sink over the tape and cut the outline with a [hobby knife](https://www.sparkfun.com/products/9200).

	<figure markdown>
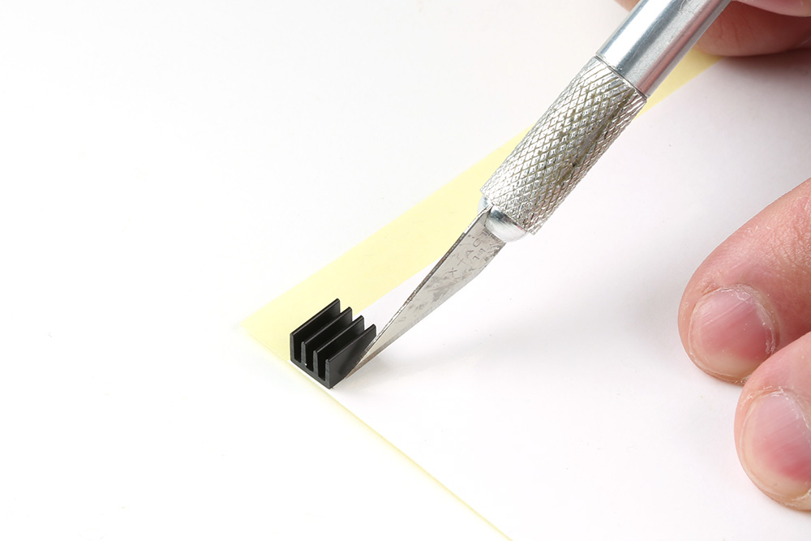
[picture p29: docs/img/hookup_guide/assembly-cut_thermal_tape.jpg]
	
	<figcaption markdown>
	Cutting the [thermal tape](https://www.sparkfun.com/products/17054) to fit the [heat sink](https://www.sparkfun.com/products/11510).
	</figcaption>
	</figure>

2. Place the piece of thermal tape on the bottom of the heat sink.

	!!! tip
		We recommend peeling off just one side of the backing sheet or [release liner](https://en.wikipedia.org/wiki/Release_liner) to place the thermal tape on the heat sink. Users can then peel the other side off when they are ready to place the heat sink on their board.
	
3. Attach the heat sink to the board.
    * Make sure to make any jumper modifications and/or solder any connections before placing the heat sink on the board.
    * Make sure to avoid any electrical contact with the sides of the heat sink.

	<figure markdown>
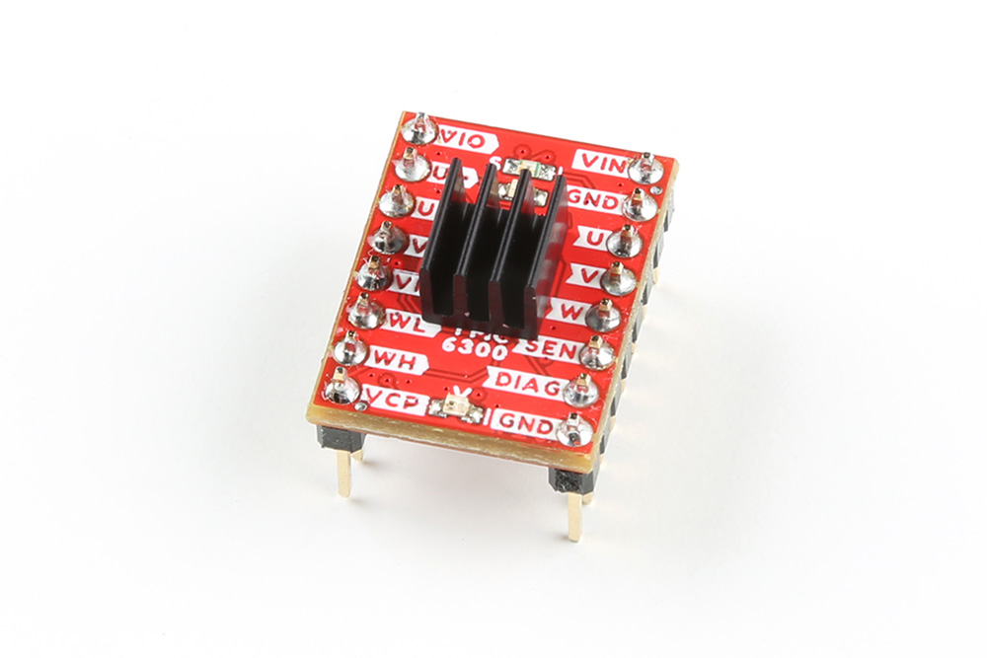
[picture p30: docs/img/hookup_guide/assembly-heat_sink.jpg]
	
	<figcaption markdown>
	[Heat sink](https://www.sparkfun.com/products/11510) attached to the TMC6300 motor driver.
	</figcaption>
	</figure>

## BLDC Gimbal Motor

!!! warning "Advanced Skills Required"
	To connect the gimbal motor to the TMC6300 motor driver board, some advanced soldering and wire stripping skills are necessary. The wire leads from the motor are only about 2" long, which is not a lot to work with. Users may only have two attempts at stripping the wires before they run out the available wire length.

??? note "New to soldering?"
	If you have never soldered before or need a quick refresher, check out our [How to Solder: Through-Hole Soldering](https://learn.sparkfun.com/tutorials/how-to-solder-through-hole-soldering) guide.
	<p align="center">
		<a href="https://learn.sparkfun.com/tutorials/5">How to Solder: Through-Hole Soldering<br>
		Tutorial's thumbnail</a>
	</p>

To connect the gimbal motor to the TMC6300 motor driver, users will need to expose the wiring. First, remove the JST connector and make sure to cut as close to the plastic housing as possible.

<figure markdown>
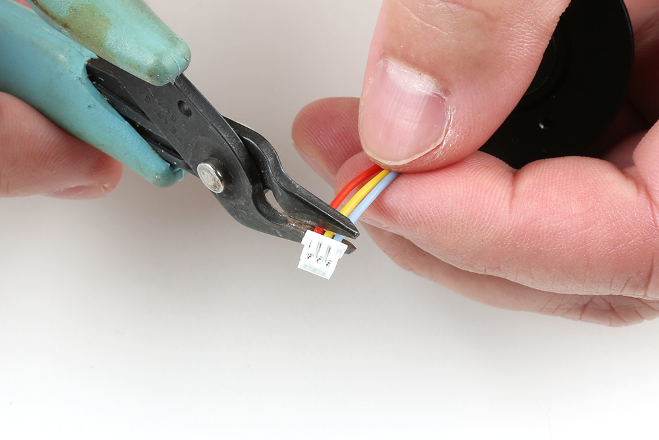
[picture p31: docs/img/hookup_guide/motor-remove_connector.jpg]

<figcaption markdown>
Cut off the plastic JST connector on the motor's wire leads.
</figcaption>
</figure>

??? info "Alternative Connections"
	If users are utilize the alligator or IC hook pigtails, they may be able to crack the plastic housing of the connector to expose the crimped wire terminals.

Next, with as much care as possible, strip off some of the electrical insulation of each of the leads. On our [wire strippers](https://www.sparkfun.com/products/15220), the 26AWG notch worked the best.

<figure markdown>
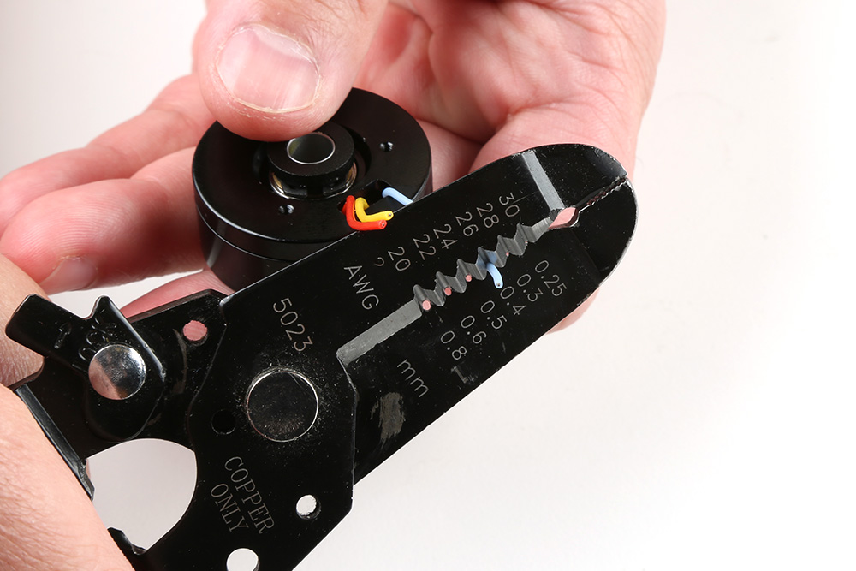
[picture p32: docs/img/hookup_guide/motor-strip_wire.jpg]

<figcaption markdown>
Strip off some of the insulation from the motor's wire leads.
</figcaption>
</figure>

The last step is to twist and tin the wires, so that they can be inserted into some jumper wires. Make sure to keep the ends straight and avoid adding to much solder, so that the wire ends can still fit into the female jumper wire terminals.

<center>
<table class="pdf">
	<tr>
		<td align="center">
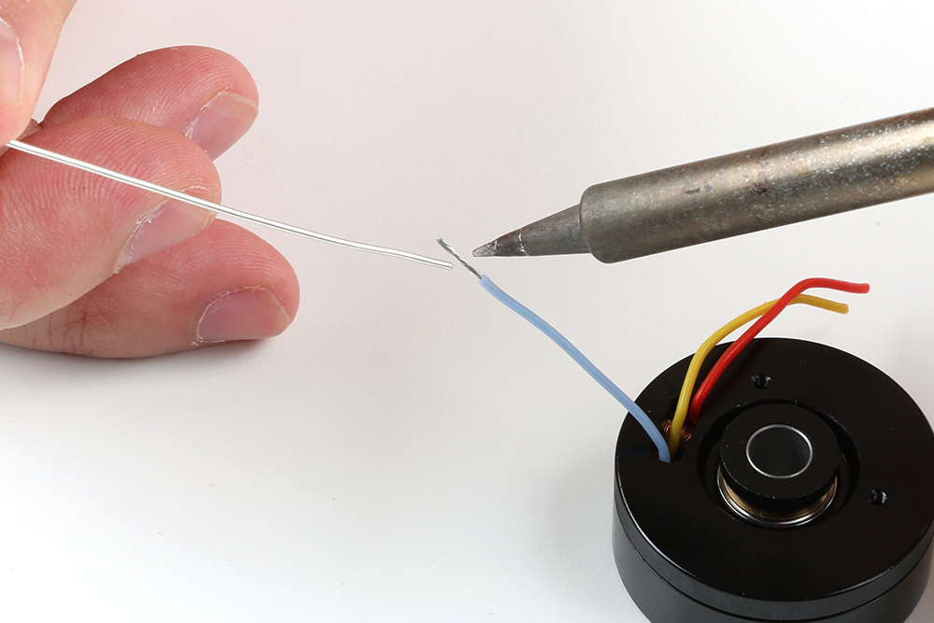
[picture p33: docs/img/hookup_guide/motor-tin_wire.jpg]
			<br>
			<i>Twist and tin the exposed wire leads, so that they can be inserted into the female end of a jumper wire.</i>
		</td>
		<td align="center">
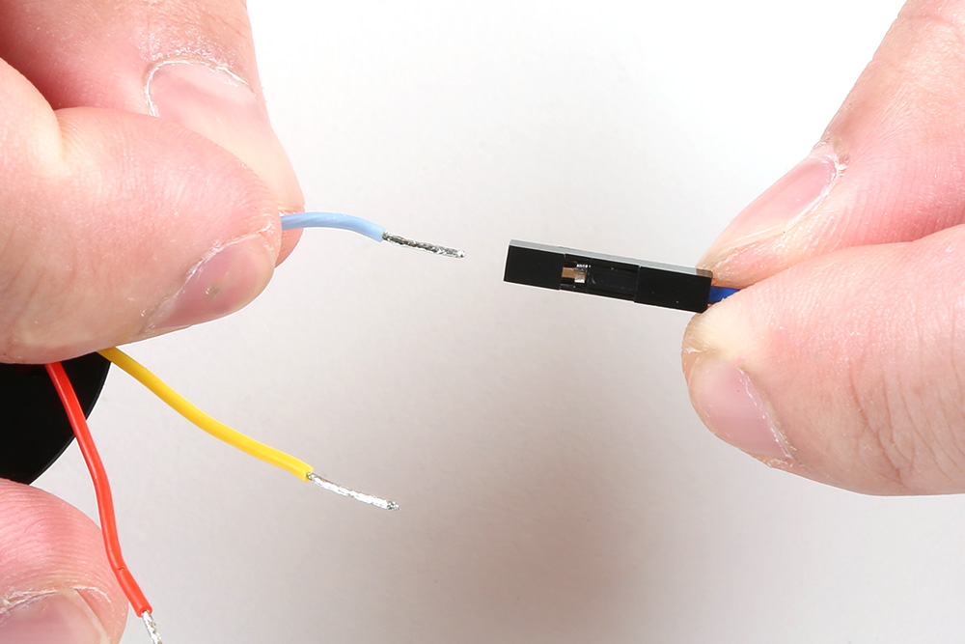
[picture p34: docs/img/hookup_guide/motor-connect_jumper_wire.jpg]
			<br>
			<i>The leads should be straight and clear of bulges fit the into female terminals.</i>
		</td>
	<tr>
</table>
</center>

<div class="grid cards hide" markdown>

-   <figure markdown>
	
	<figcaption markdown>
	Twist and tin the exposed wire leads, so that they can be inserted into the femal end of a jumper wire.
	</figcaption>
	</figure>

-   <figure markdown>
	
	<figcaption markdown>
	The leads should be straight and clear of bulges fit the female terminals of the jumper wire.
	</figcaption>
	</figure>

</div>

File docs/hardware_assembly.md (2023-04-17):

---
icon: material/tools
---

## Assembly for Examples
The following instructions are for wiring up the RedBoard Plus, TMC6300 motor driver, and motor for the examples provided in this tutorial. 

### RedBoard Plus to TMC6300

For ease of use, connect the TMC6300 motor driver with headers attached to the center of breadboard. The pin layout should perfectly align, so that users will have three breadboard pins available on each side of the TMC6300 breakout board. Then, following the table below, connect the pins from the RedBoard Plus to breadboard pins associated with the motor driver.

<center>

| RedBoard | `3`  | `5`  | `6`  | `9`  | `10` | `11` | `12`  | `GND` |
| :--- | :--: | :--: | :--: | :--: | :--: | :--: | :---: | :---: |
| Motor Driver | `UL` | `WL` | `WH` | `VL` | `VH` | `UH` | `VIO` | `GND` |

</center>

<figure markdown>
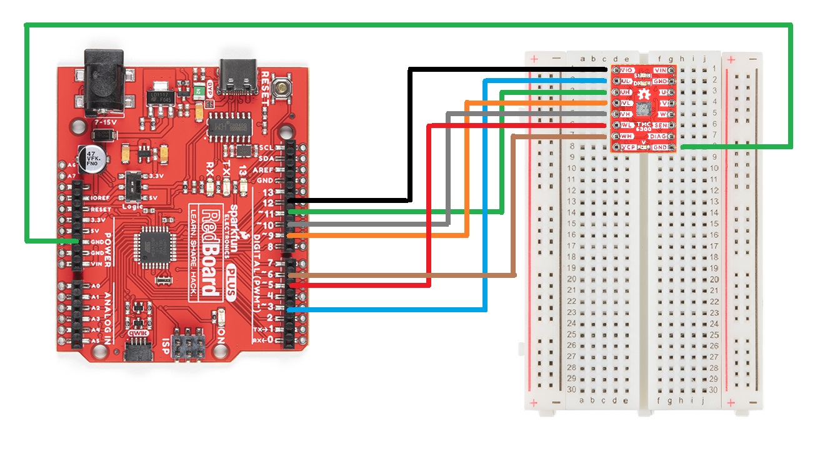
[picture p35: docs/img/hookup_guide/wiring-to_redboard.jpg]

<figcaption markdown>
A graphical representation of the connections between the [RedBoard Plus](https://www.sparkfun.com/products/18158) and a [breadboard](https://www.sparkfun.com/products/12002) with the [TMC6300 motor driver](https://www.sparkfun.com/products/21867) attached.
</figcaption>
</figure>

!!! info "Timer Pins"
	As mentioned in the [Simple FOC library documentation](https://docs.simplefoc.com/bldcdriver6pwm#arduino-uno-support), 

	<blockquote markdown>
	--8<-- "https://raw.githubusercontent.com/simplefoc/simplefoc.github.io/master/docs/simplefoc_library/code/drivers/bldc_driver/bldc_driver_6pwm.md:41:50"
	</blockquote>

### Motor to TMC6300

Connecting a motor to the TMC6300 motor driver straight forward. Users, just need to connect the half-bridge drive channels with the ends of the motor's stator coils.

* [Utilizing two half-bridges to drive a brushed DC motor with a full H-bridge](https://fab.cba.mit.edu/classes/865.21/topics/power_electronics/architectures/#h-bridges)
* [Utilizing three half-bridges to drive a brushless DC motor](https://fab.cba.mit.edu/classes/865.21/topics/power_electronics/architectures/#triple-half-bridges)

#### BLDC Gimbal Motor

Connecting a 3-phase, [BLDC](https://en.wikipedia.org/wiki/Brushless_DC_electric_motor "brushless DC") motor to the motor driver is relatively simple as the sequence of the wires connection doesn't matter. Using jumper wires, connect the [prepared ends of the gimbal stabilizer motor](../component_assembly/#bldc-gimbal-motor) to the [`U`, `V`, and `W` pins of the TMC6300 breakout board](../hardware_overview/#__tabbed_1_2).

<figure markdown>

<figcaption markdown>
A prepared end of the gimbal motor being inserted into the female terminals of a jumper wire.
</figcaption>
</figure>

!!! tip 
	Users may want to prop up the base of the gimbal motor, as the magnetic end of the motor shaft protudes below its base plate. Users can see a demonstration in the video below:

	<center>
	[:material-youtube:{ .heart } Video with Gimbal Motor ](https://youtu.be/Q76dMggUH1M?t=233){ .md-button .md-button--primary }
	</center>

??? info "Reversing the Rotation of the Motor"
	For a 3-phase brushless motor, the connection sequence of the wires to a BLDC motor doesn't necessarily matter; the direction that the motor spins can be controlled through the software. However, for reference, switching two of the output channels to the motor will automatically reverse the direction that the motor was spinning.

	* If users swap just the `U` and `V` connections, leaving the `W` connection alone, the motor will now spin in the opposite direction of the original configuration.

#### DC Hobby Motor

If this was a H-bridge motor driver, the connections to the motor wouldn't matter. However, as there are three half-bridges, users will need to note which half-bridges the DC motor is connected to. These connections will dictate how the motor is driven by the software. For the example, connect the motor to the `V` and `W` output channels of the TMC6300 motor driver.

??? info "Reversing the Rotation of the Motor"
	For a  single phase DC motor, the direction that the motor spins can be controlled through the software. However, for reference, switching the polarity of the motor's wires will also reverse the direction that the motor was spinning.

### Powering the TMC6300

Enough power should be provided to the TMC6300 to drive the motor connected to it. Therefore, the drive current and voltage range of the motor should be taken into consideration. Additionally, users should monitor the drive current to prevent overheating of the TMC6300 motor driver.

Ideally, if users have access to a variable power supply, it would be the most convenient solution for adjusting the voltage and source current parameters. Other power supply alternatives include a 6V (4xAA) battery pack or dual-cell LiPo battery. However, if users are unable to find a suitable power source, we have found that the 5V power output from the RedBoard Plus is sufficient to drive the gimbal motor, under a no load condition at low speeds.

<center>

| RedBoard | `5V`  | `GND` |
| :--- | :---: | :---: |
| Motor Driver | `VIN` | `GND` |

</center>

<figure markdown>
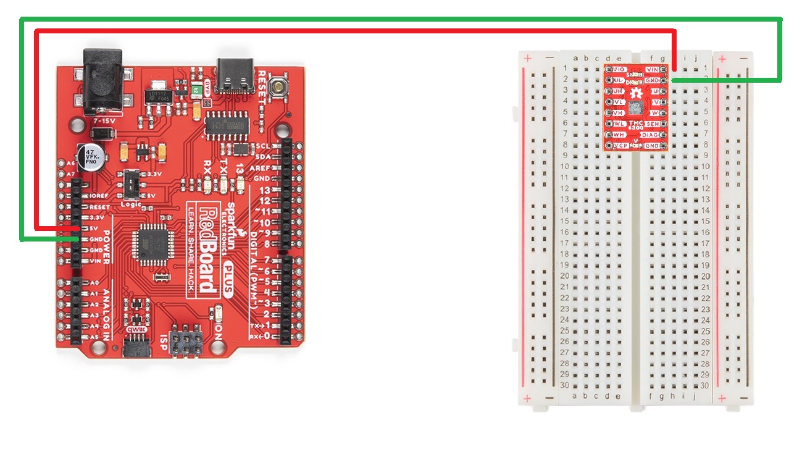
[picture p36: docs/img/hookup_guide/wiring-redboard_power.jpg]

<figcaption markdown>
A graphical representation of the connections between the [RedBoard Plus](https://www.sparkfun.com/products/18158) and a [breadboard](https://www.sparkfun.com/products/12002) with the [TMC6300 motor driver](https://www.sparkfun.com/products/21867) attached.
</figcaption>
</figure>

??? tip "Current Monitoring"
	For the examples in this tutorial, the motor will be driven with a no-load condition and the motor drive current shouldn't need to be monitored. *(An exception would be when the motor is hindered from spinning, in which case the torque and drive current will spike.)*

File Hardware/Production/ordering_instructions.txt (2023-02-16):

panel size, 108x118mm
PCB thickness, 1.6mm
number of layers, 2
soldermask color, Red
silkscreen color, White
oz copper, 1oz
finish, HASL lead free
stencils, top+bottom
pcs per panel, 30
min trace width, 0.1778mm / 0.0070in
min drill size, 0.3048mm / 0.0120in

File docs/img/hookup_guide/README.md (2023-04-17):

img/hookup_guide directory
====================
This folder should contain the images for the hookup guide pages

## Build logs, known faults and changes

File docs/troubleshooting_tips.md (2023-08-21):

---
icon: sfe-logo
---

!!! warning "Need Help?"
    If you need technical assistance or more information on a product that is not working as you expected, we recommend heading on over to the [SparkFun Technical Assistance](https://www.sparkfun.com/technical_assistanc) page for some initial troubleshooting.

    <center>
    [SparkFun Technical Assistance Page](https://www.sparkfun.com/technical_assistance){ .md-button .md-button--primary }
    </center>
    
    If you can't find what you need there, the [SparkFun Forums](https://forum.sparkfun.com/index.php) is a great place to search product forums and ask questions.
    
    !!! info "Account Registration Required"
        If this is your first visit to our forum, you'll need to create a [Forum Account](https://forum.sparkfun.com/ucp.php?mode=register) to post questions.

## ESP32 Compile Error
If users run into an error similar to, `fatal error: soc/soc_caps.h: No such file or directory`, it may be due to an issue with the version of the ESP32 Arduino core that is installed in the **Boards Manager**. Users should make sure the have the latest version of the ESP32 Arduino core installed; or at least a version later than `v2.0.1`.

!!! info
    For more information, please reference this [forum post](https://community.simplefoc.com/t/compilation-error/1700) for the Simple FOC Arduino library.

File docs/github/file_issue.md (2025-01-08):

# Did we make a mistake?

Spot something wrong? Please let us know. 

<!-- Technical Assistance Box -->
!!! warning "Need Help?"
    If you need technical assistance or more information on a product that is not working as you expected, we recommend heading on over to the [SparkFun Technical Assistance](https://www.sparkfun.com/technical_assistance) page for some initial troubleshooting. This **Submit Issues** page is not where users should seek assistance.

    <center>
    [SparkFun Technical Assistance Page](https://www.sparkfun.com/technical_assistance){ .md-button .md-button--primary }
    </center>
    
    If you can't find what you need there, the [SparkFun Forums](https://forum.sparkfun.com/index.php) is a great place to search the product forums and ask questions.
    
    !!! info "Account Registration Required"
        For your first visit to our forum, you'll need to create a [Forum Account](https://forum.sparkfun.com/ucp.php?mode=register) to post questions.

## Discrepancies in the Documentation

All of our documentation can be modified by you! Please help us make it better.

* The documentation files for these pages are contained in the [`docs` folder](https://github.com/sparkfun/SparkFun_Three_Phase_Motor_Driver-TMC6300/tree/main/docs) of the [SparkFun TMC6300 motor driver repository](https://github.com/sparkfun/SparkFun_Three_Phase_Motor_Driver-TMC6300).

### 🔍 Spot something wrong?

If a section of the documentation is incorrect, please [open an issue](https://github.com/sparkfun/SparkFun_Three_Phase_Motor_Driver-TMC6300/issues) and let us know.

### Do you have a suggested correction?

1. With a GitHub account, [fork this repository](https://github.com/sparkfun/SparkFun_Three_Phase_Motor_Driver-TMC6300/fork).
2. Add your correction(s) or improvement(s) to the markdown file(s)
3. File a pull request with your changes, and enjoy making the ~~words~~ ~~worlds~~ world a better place.
	* Once received, the documentation specialist will automatically be notified.
	* We will review your suggested improvement(s) to make sure they are correct and fit within our documentation standards.

## Problems in the Hardware Design

All of our designs are open-source! Please help us make it better.

* Our board design files are contained in the [`Hardware` folder](https://github.com/sparkfun/SparkFun_Three_Phase_Motor_Driver-TMC6300/tree/main/Hardware) of the [SparkFun TMC6300 motor driver repository](https://github.com/sparkfun/SparkFun_Three_Phase_Motor_Driver-TMC6300).

### Does something not make sense? 🤔

If part of the design is confusing, please [open an issue](https://github.com/sparkfun/SparkFun_Three_Phase_Motor_Driver-TMC6300/issues) and let us know.

### Did we forget to include an important function of the board? 🤦

If part of the board's functionality is missing, please [open an issue](https://github.com/sparkfun/SparkFun_Three_Phase_Motor_Driver-TMC6300/issues) and file a feature request.

!!! tip "Design Considerations"
	Please keep in mind that we may intentionally exclude certain functions of the board to meet our product design requirements.
	
	* *For example, our Qwiic Micro boards are intended to fit on a small board layout and only use I<sup>2</sup>C communication; therefore, we may not have the SPI and interrupt pins available for users.*

### Do you wish to contribute directly to improving the board design?

1. With a GitHub account, [fork this repository](https://github.com/sparkfun/SparkFun_Three_Phase_Motor_Driver-TMC6300/fork).
2. Add your design augmentation(s)
3. File a pull request with your changes, and enjoy making the ~~words~~ ~~worlds~~ world a better place.
	1. Once received, the engineer in charge of the original design will automatically be notified.
	2. We will review your suggested improvement(s) to verify that they are within our board design standards and meet our product design requirements.
	3. If approved, we will flag these changes for our next board revision. Congrats! 🍻

		!!! info
			Even if your suggestion is accepted, these changes may not be immediately available for purchase. We may have to cycle through our current product inventory first.

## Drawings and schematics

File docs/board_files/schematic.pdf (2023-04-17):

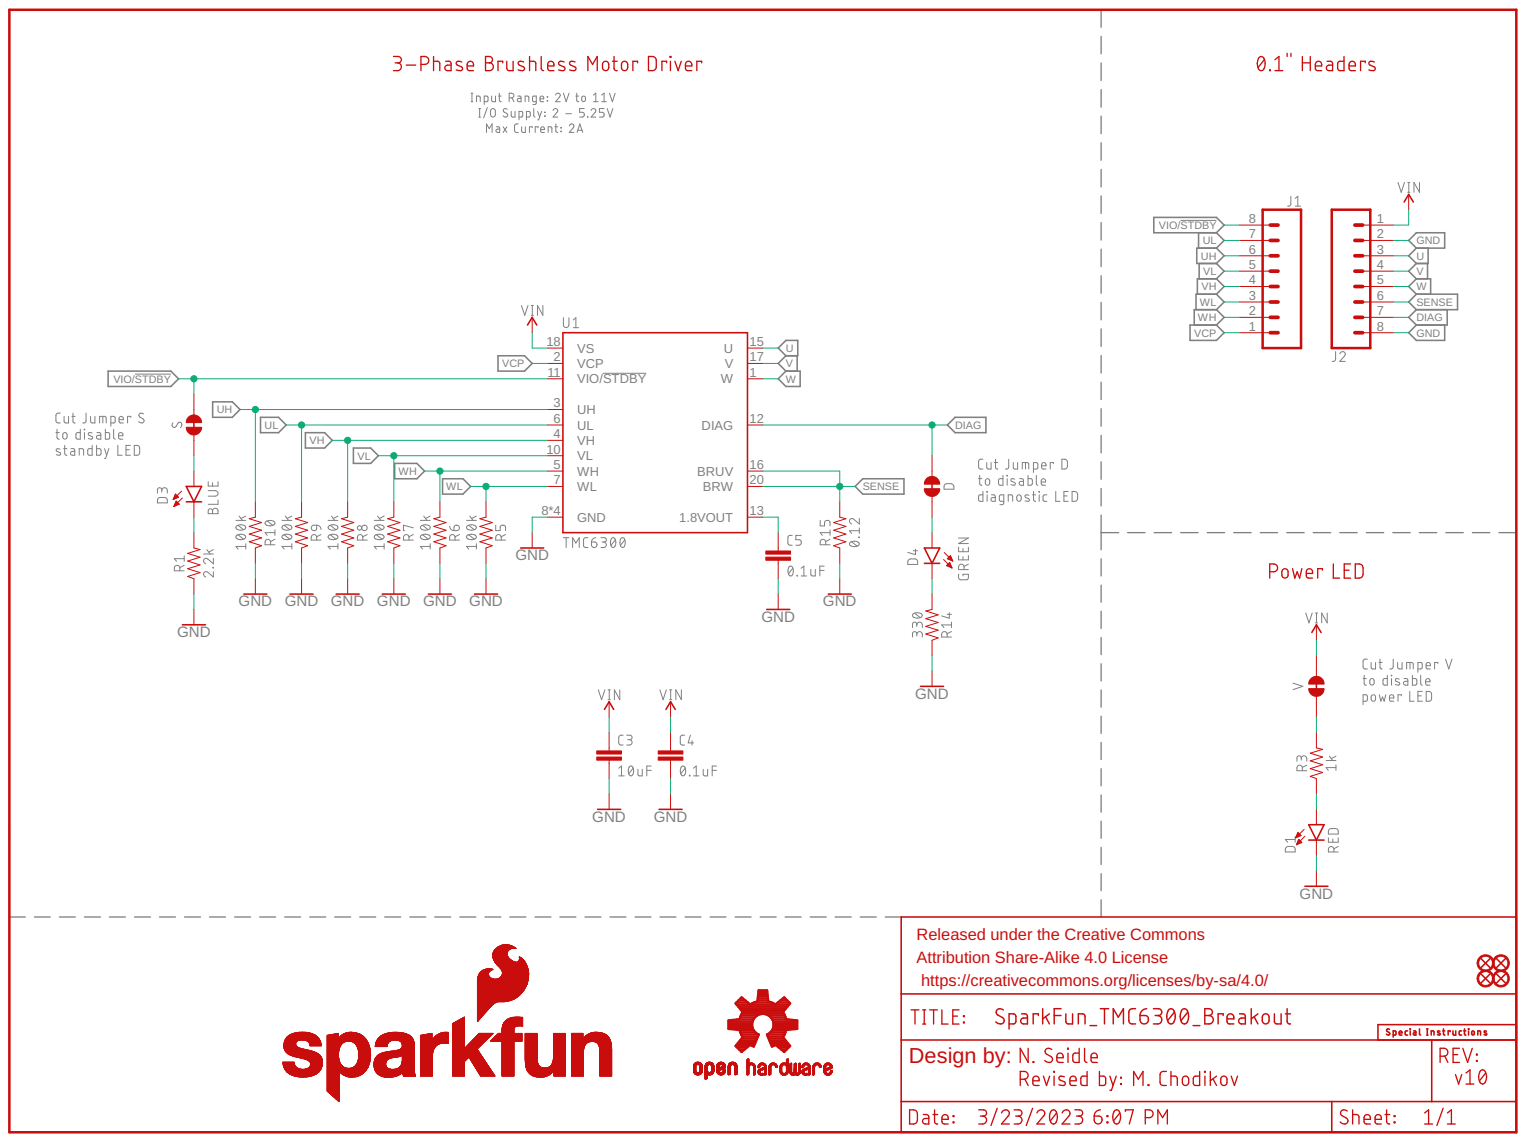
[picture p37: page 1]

GND GND GND

Released under the Creative Commons
Attribution Share-Alike 4.0 License
https://creativecommons.org/licenses/by-sa/4.0/

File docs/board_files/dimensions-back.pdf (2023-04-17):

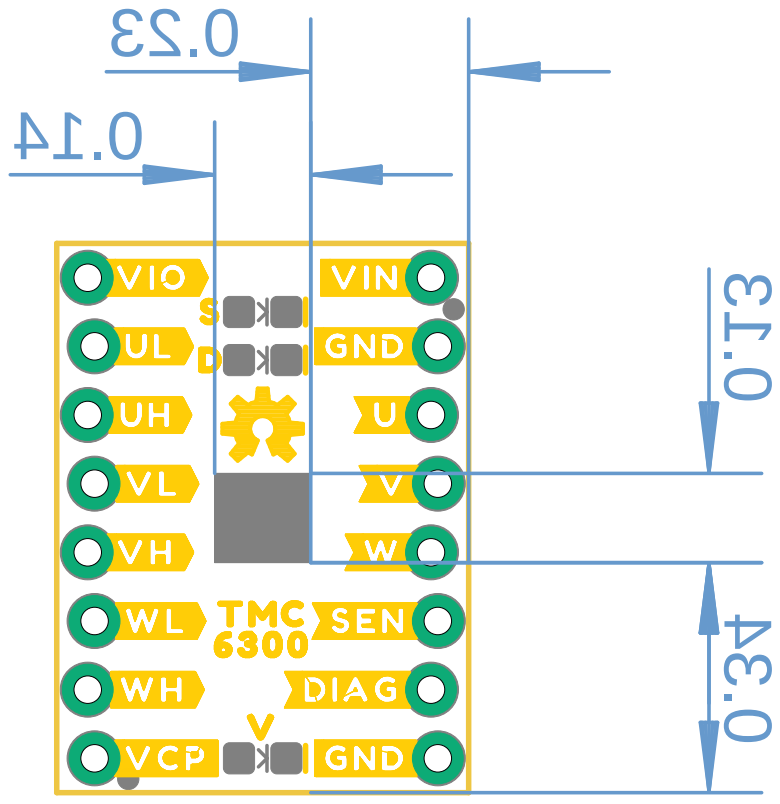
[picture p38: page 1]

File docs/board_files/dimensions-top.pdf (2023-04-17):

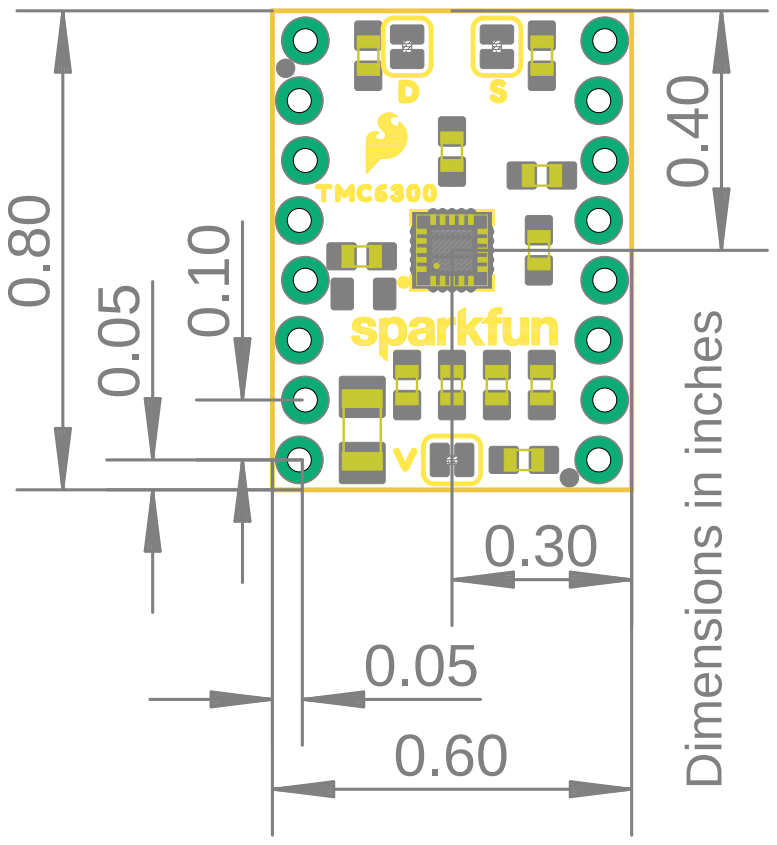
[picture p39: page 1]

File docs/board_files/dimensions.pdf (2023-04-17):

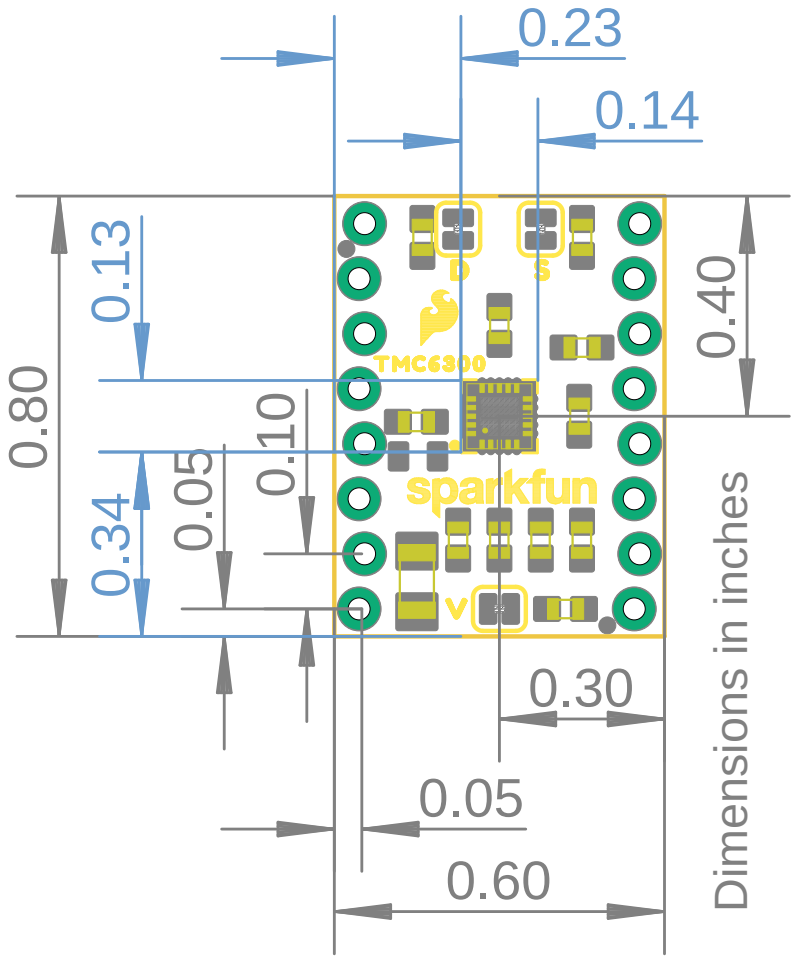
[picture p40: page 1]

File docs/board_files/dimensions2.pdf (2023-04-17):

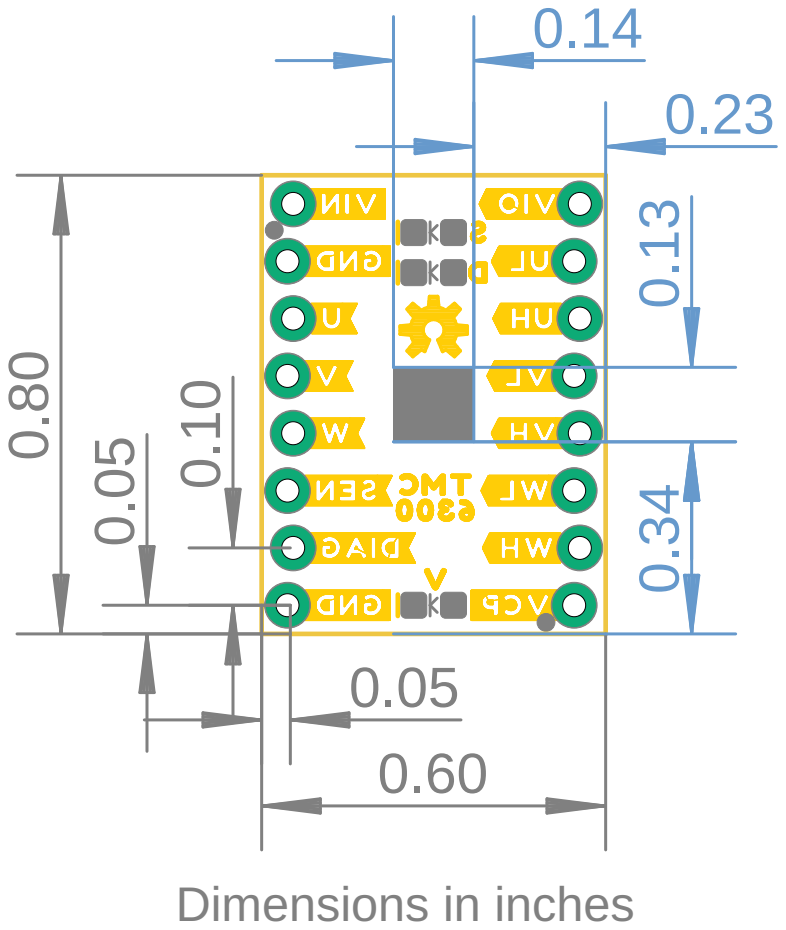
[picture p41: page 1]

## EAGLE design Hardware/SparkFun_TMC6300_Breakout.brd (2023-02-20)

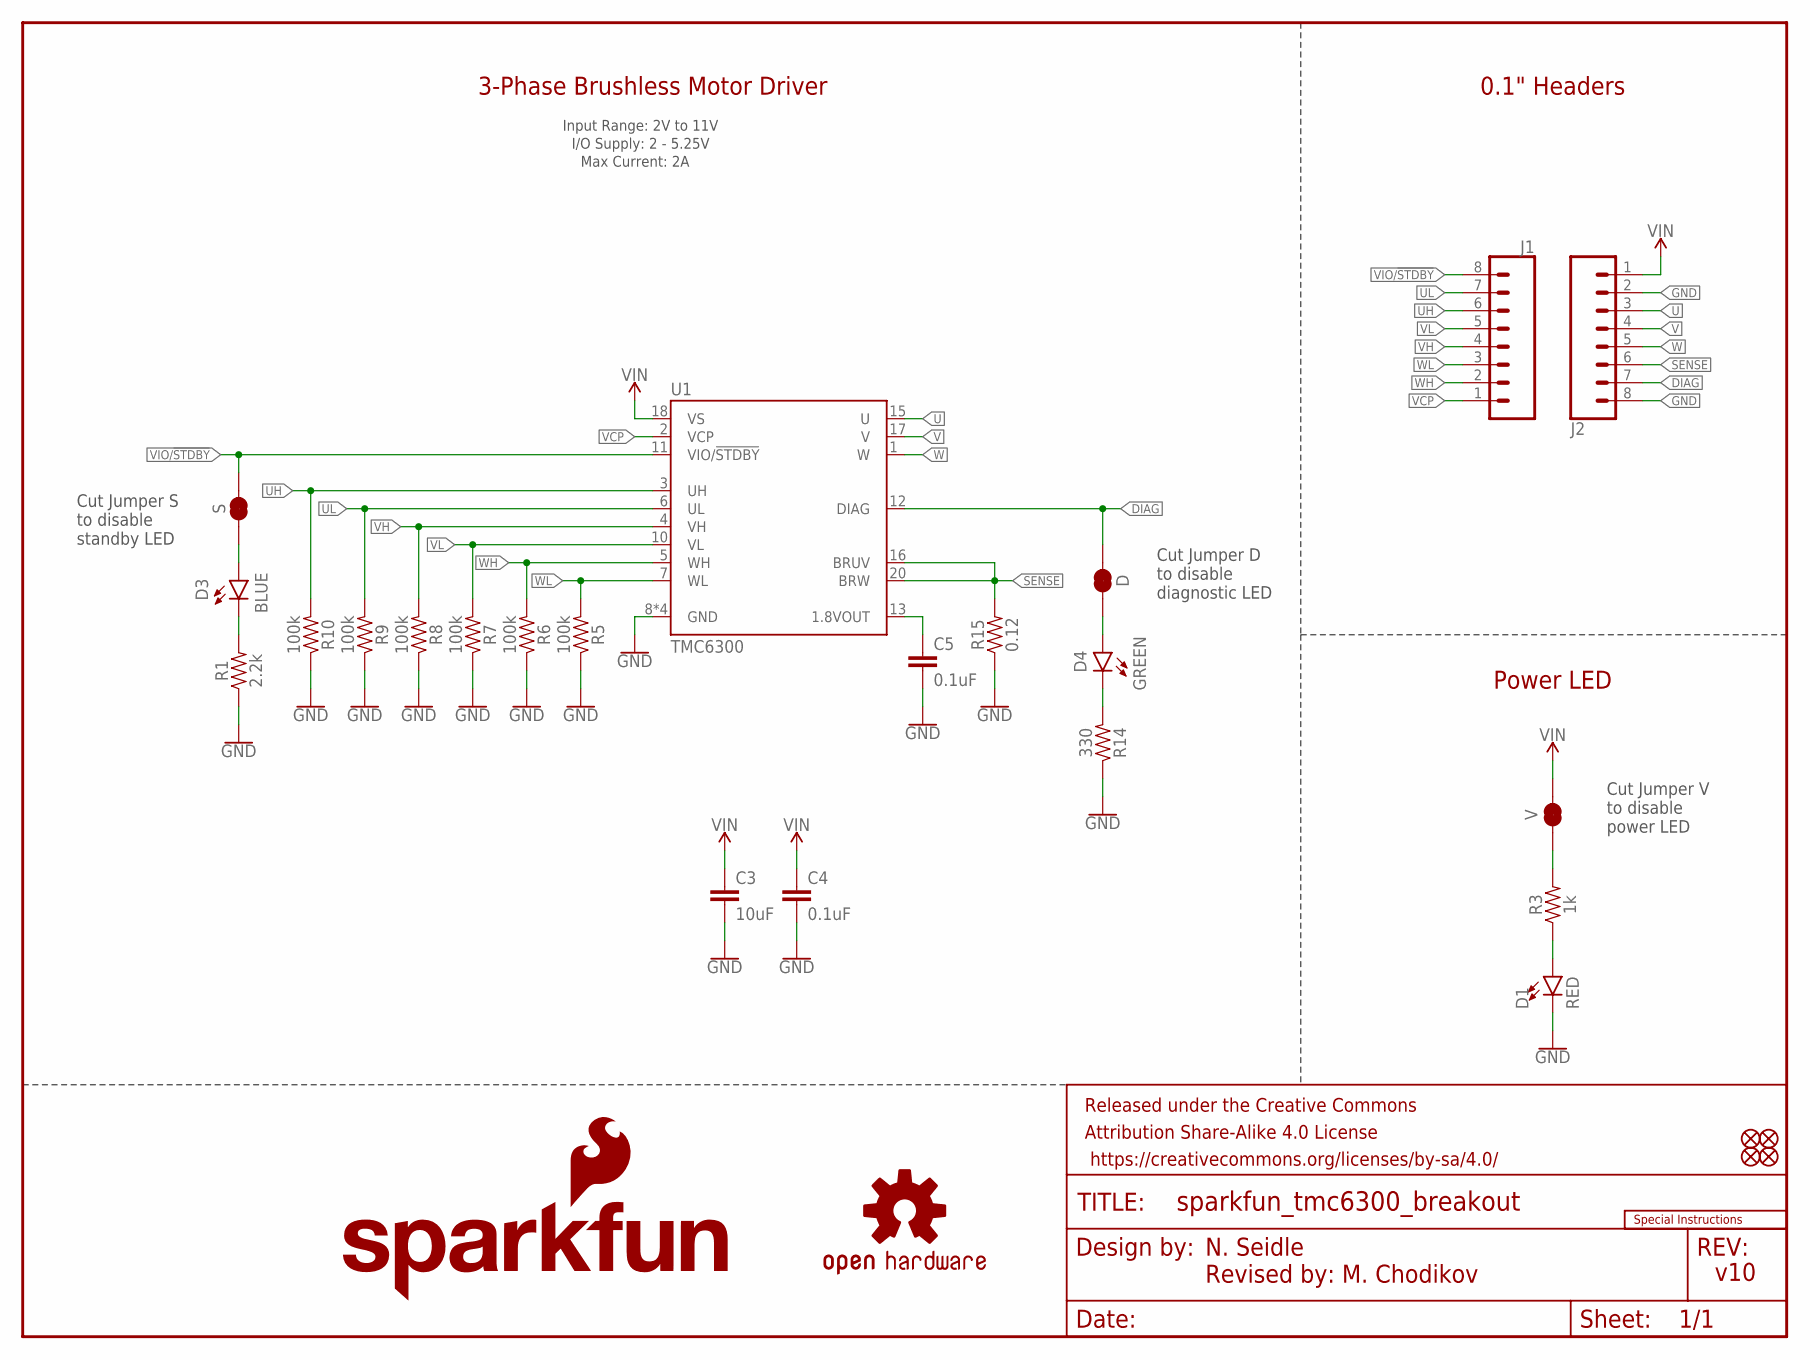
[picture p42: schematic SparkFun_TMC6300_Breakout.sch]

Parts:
C3: 10uF; 0805
C4, C5: 0.1uF; 0603
D: JUMPER-SMT_2_NC_TRACE_SILK; SMT-JUMPER_2_NC_TRACE_SILK
D1: RED; LED-0603
D3: BLUE; LED-0603
D4: GREEN; LED-0603
FD1, FD2, FD3, FD4: FIDUCIALUFIDUCIAL; FIDUCIAL-MICRO
FRAME1: FRAME-LETTER; CREATIVE_COMMONS
J1, J2: CONN_08LOCK_NO_SILK; 1X08_LOCK_NO_SILK
LOGO2: SPECIAL_INSTRUCTIONS-ORDERING; ORDERING_INSTRUCTIONS
LOGO3: SFE_LOGO_NAME.08_INCH; SFE_LOGO_NAME_.08
LOGO4: SFE_LOGO_FLAME.1_INCH; SFE_LOGO_FLAME_.1
LOGO5: OSHW-LOGOS; OSHW-LOGO-S
R1: 2.2k; 0603
R3: 1k; 0603
R5, R6, R7, R8, R9, R10: 100k; 0603
R14: 330; 0603
R15: 0.12; 1206
S: JUMPER-SMT_2_NC_TRACE_SILK; SMT-JUMPER_2_NC_TRACE_SILK
U1: TMC6300; QFN-20
V: JUMPER-SMT_2_NC_TRACE_SILK; SMT-JUMPER_2_NC_TRACE_SILK

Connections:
DIAG: D.2, J2.7, U1.12 (DIAG)
GND: C3.2, C4.2, C5.2, D1.C, J2.2, J2.8, R1.1, R5.1, R6.1, R7.1, R8.1, R9.1, R10.1, R14.1, R15.1, U1.8 (GND), U1.9 (GND), U1.14 (GND), U1.PAD (GND)
unnamed: R3.2, V.1
unnamed: D1.A, R3.1
unnamed: D3.A, S.1
unnamed: C5.1, U1.13 (1.8VOUT)
unnamed: D.1, D4.A
unnamed: D3.C, R1.2
unnamed: D4.C, R14.2
SENSE: J2.6, R15.2, U1.16 (BRUV), U1.20 (BRW)
U: J2.3, U1.15 (U)
UH: J1.6, R10.2, U1.3 (UH)
UL: J1.7, R9.2, U1.6 (UL)
V: J2.4, U1.17 (V)
VCP: J1.1, U1.2 (VCP)
VH: J1.4, R8.2, U1.4 (VH)
VIN: C3.1, C4.1, J2.1, U1.18 (VS), V.2
VIO/!STDBY!: J1.8, S.2, U1.11 (VIO/!STDBY!)
VL: J1.5, R7.2, U1.10 (VL)
W: J2.5, U1.1 (W)
WH: J1.2, R6.2, U1.5 (WH)
WL: J1.3, R5.2, U1.7 (WL)

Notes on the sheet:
0.1" Headers
Power LED
I/O Supply: 2 - 5.25V
3-Phase Brushless Motor Driver
N. Seidle
v10
Revised by: M. Chodikov
Input Range: 2V to 11V
Max Current: 2A
Cut Jumper S to disable standby LED
Cut Jumper D to disable diagnostic LED
Cut Jumper V to disable power LED

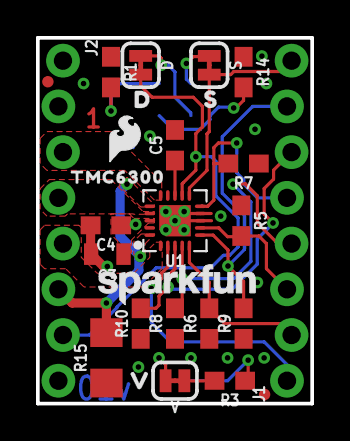
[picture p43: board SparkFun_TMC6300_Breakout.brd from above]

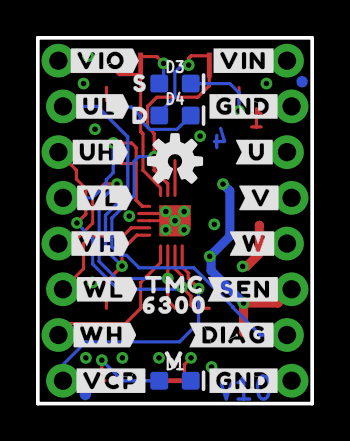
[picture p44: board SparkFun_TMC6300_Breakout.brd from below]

Board: 4 copper layers, 15.2 x 20.3 mm, 56 parts (27 on the bottom side), 22 nets.

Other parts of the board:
U$1, U$28: #GND#1
U$2: #SEN#0
U$3: #DIAG#0
U$4: TMC630063003454
U$9: #U#6
U$12: #VCP#0
U$13: #VIO#1
U$15: 63001
U$16, U$18: D0
U$19, U$27: S1
U$20, U$26: V2
U$21: #UH#5
U$22: #UL#4
U$23: TMC0
U$24: #VIN#0
U$25: #V#7
U$30: #VH#2
U$31: #VL#3
U$32: #W#8
U$33: #WH#1
U$34: #WL#0

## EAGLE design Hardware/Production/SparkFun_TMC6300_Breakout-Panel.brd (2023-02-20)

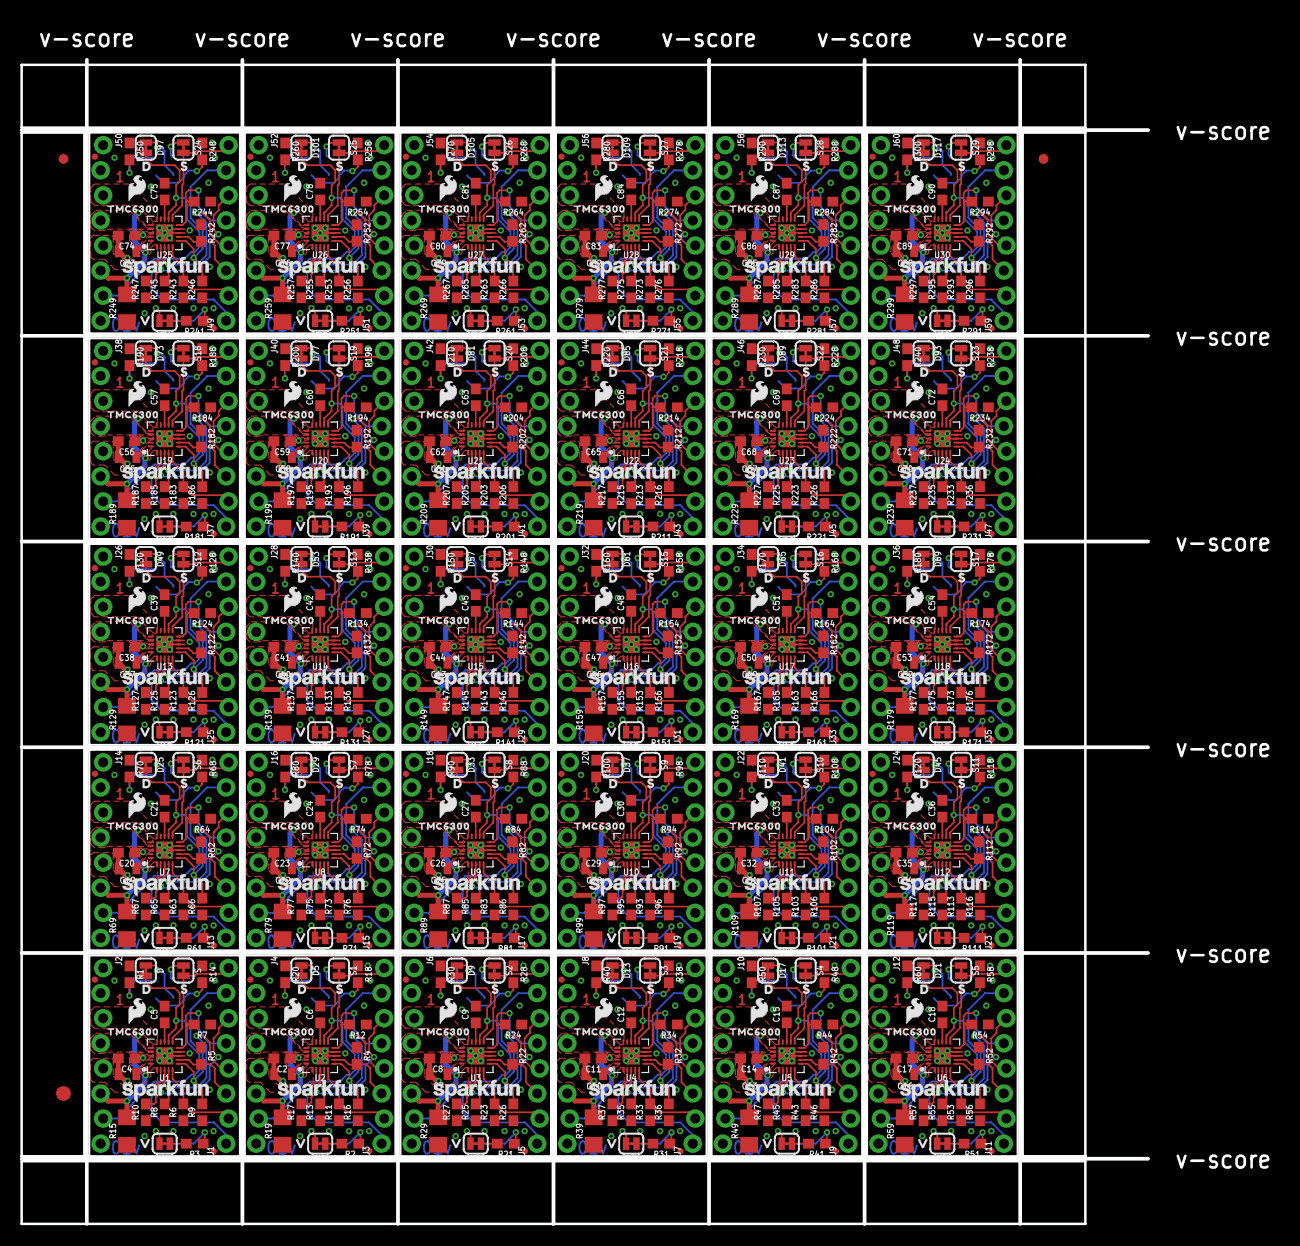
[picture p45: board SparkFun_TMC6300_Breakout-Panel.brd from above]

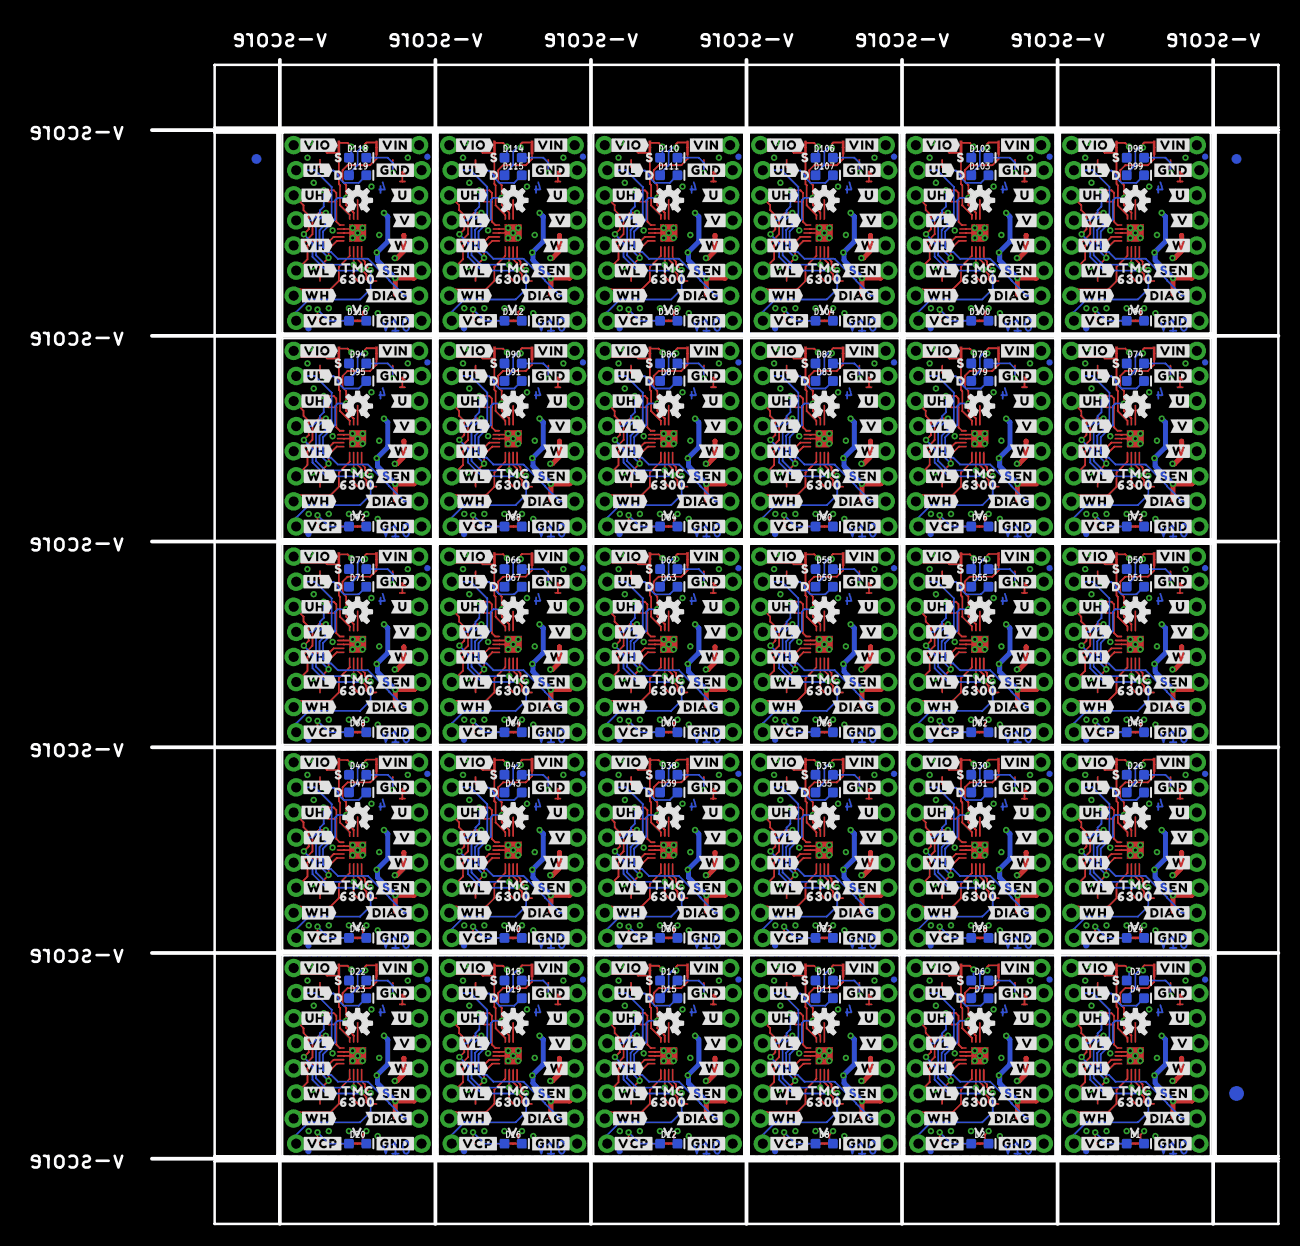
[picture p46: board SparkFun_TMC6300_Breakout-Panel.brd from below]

Board: 4 copper layers, 114.0 x 117.9 mm, 1626 parts (813 on the bottom side), 660 nets.

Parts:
C1, C3, C7, C10, C13, C16, C19, C22, C25, C28, C31, C34, C37, C40, C43, C46, C49, C52, C55, C58, C61, C64, C67, C70, C73, C76, C79, C82, C85, C88: 10uF; 0805
C2, C4, C5, C6, C8, C9, C11, C12, C14, C15, C17, C18, C20, C21, C23, C24, C26, C27, C29, C30, C32, C33, C35, C36, C38, C39, C41, C42, C44, C45, C47, C48, C50, C51, C53, C54, C56, C57, C59, C60, C62, C63, C65, C66, C68, C69, C71, C72, C74, C75, C77, C78, C80, C81, C83, C84, C86, C87, C89, C90: 0.1uF; 0603
D, D5, D9, D13, D17, D21, D25, D29, D33, D37, D41, D45, D49, D53, D57, D61, D65, D69, D73, D77, D81, D85, D89, D93, D97, D101, D105, D109, D113, D117: JUMPER-SMT_2_NC_TRACE_SILK; SMT-JUMPER_2_NC_TRACE_SILK
D1, D2, D8, D12, D16, D20, D24, D28, D32, D36, D40, D44, D48, D52, D56, D60, D64, D68, D72, D76, D80, D84, D88, D92, D96, D100, D104, D108, D112, D116: RED; LED-0603
D3, D6, D10, D14, D18, D22, D26, D30, D34, D38, D42, D46, D50, D54, D58, D62, D66, D70, D74, D78, D82, D86, D90, D94, D98, D102, D106, D110, D114, D118: BLUE; LED-0603
D4, D7, D11, D15, D19, D23, D27, D31, D35, D39, D43, D47, D51, D55, D59, D63, D67, D71, D75, D79, D83, D87, D91, D95, D99, D103, D107, D111, D115, D119: GREEN; LED-0603
E$1, E$2, E$3, E$4: FIDUCIAL-1X2
E$5, E$6: FIDUCIAL-1.5X3
FD1, FD2, FD3, FD4, FD5, FD6, FD7, FD8, FD9, FD10, FD11, FD12, FD13, FD14, FD15, FD16, FD17, FD18, FD19, FD20, FD21, FD22, FD23, FD24, FD25, FD26, FD27, FD28, FD29, FD30, FD31, FD32, FD33, FD34, FD35, FD36, FD37, FD38, FD39, FD40, FD41, FD42, FD43, FD44, FD45, FD46, FD47, FD48, FD49, FD50, FD51, FD52, FD53, FD54, FD55, FD56, FD57, FD58, FD59, FD60, FD61, FD62, FD63, FD64, FD65, FD66, FD67, FD68, FD69, FD70, FD71, FD72, FD73, FD74, FD75, FD76, FD77, FD78, FD79, FD80, FD81, FD82, FD83, FD84, FD85, FD86, FD87, FD88, FD89, FD90, FD91, FD92, FD93, FD94, FD95, FD96, FD97, FD98, FD99, FD100, FD101, FD102, FD103, FD104, FD105, FD106, FD107, FD108, FD109, FD110, FD111, FD112, FD113, FD114, FD115, FD116, FD117, FD118, FD119, FD120: FIDUCIALUFIDUCIAL; FIDUCIAL-MICRO
J1, J2, J3, J4, J5, J6, J7, J8, J9, J10, J11, J12, J13, J14, J15, J16, J17, J18, J19, J20, J21, J22, J23, J24, J25, J26, J27, J28, J29, J30, J31, J32, J33, J34, J35, J36, J37, J38, J39, J40, J41, J42, J43, J44, J45, J46, J47, J48, J49, J50, J51, J52, J53, J54, J55, J56, J57, J58, J59, J60: 1X08_LOCK_NO_SILK
LOGO1, LOGO3, LOGO7, LOGO10, LOGO13, LOGO16, LOGO19, LOGO22, LOGO25, LOGO28, LOGO31, LOGO34, LOGO37, LOGO40, LOGO43, LOGO46, LOGO49, LOGO52, LOGO55, LOGO58, LOGO61, LOGO64, LOGO67, LOGO70, LOGO73, LOGO76, LOGO79, LOGO82, LOGO85, LOGO88: SFE_LOGO_NAME.08_INCH; SFE_LOGO_NAME_.08
LOGO2, LOGO4, LOGO8, LOGO11, LOGO14, LOGO17, LOGO20, LOGO23, LOGO26, LOGO29, LOGO32, LOGO35, LOGO38, LOGO41, LOGO44, LOGO47, LOGO50, LOGO53, LOGO56, LOGO59, LOGO62, LOGO65, LOGO68, LOGO71, LOGO74, LOGO77, LOGO80, LOGO83, LOGO86, LOGO89: SFE_LOGO_FLAME.1_INCH; SFE_LOGO_FLAME_.1
LOGO5, LOGO6, LOGO9, LOGO12, LOGO15, LOGO18, LOGO21, LOGO24, LOGO27, LOGO30, LOGO33, LOGO36, LOGO39, LOGO42, LOGO45, LOGO48, LOGO51, LOGO54, LOGO57, LOGO60, LOGO63, LOGO66, LOGO69, LOGO72, LOGO75, LOGO78, LOGO81, LOGO84, LOGO87, LOGO90: OSHW-LOGOS; OSHW-LOGO-S
R1, R20, R30, R40, R50, R60, R70, R80, R90, R100, R110, R120, R130, R140, R150, R160, R170, R180, R190, R200, R210, R220, R230, R240, R250, R260, R270, R280, R290, R300: 2.2k; 0603
R2, R3, R21, R31, R41, R51, R61, R71, R81, R91, R101, R111, R121, R131, R141, R151, R161, R171, R181, R191, R201, R211, R221, R231, R241, R251, R261, R271, R281, R291: 1k; 0603
R4, R5, R6, R7, R8, R9, R10, R11, R12, R13, R16, R17, R22, R23, R24, R25, R26, R27, R32, R33, R34, R35, R36, R37, R42, R43, R44, R45, R46, R47, R52, R53, R54, R55, R56, R57, R62, R63, R64, R65, R66, R67, R72, R73, R74, R75, R76, R77, R82, R83, R84, R85, R86, R87, R92, R93, R94, R95, R96, R97, R102, R103, R104, R105, R106, R107, R112, R113, R114, R115, R116, R117, R122, R123, R124, R125, R126, R127, R132, R133, R134, R135, R136, R137, R142, R143, R144, R145, R146, R147, R152, R153, R154, R155, R156, R157, R162, R163, R164, R165, R166, R167, R172, R173, R174, R175, R176, R177, R182, R183, R184, R185, R186, R187, R192, R193, R194, R195, R196, R197, R202, R203, R204, R205, R206, R207, R212, R213, R214, R215, R216, R217, R222, R223, R224, R225, R226, R227, R232, R233, R234, R235, R236, R237, R242, R243, R244, R245, R246, R247, R252, R253, R254, R255, R256, R257, R262, R263, R264, R265, R266, R267, R272, R273, R274, R275, R276, R277, R282, R283, R284, R285, R286, R287, R292, R293, R294, R295, R296, R297: 100k; 0603
R14, R18, R28, R38, R48, R58, R68, R78, R88, R98, R108, R118, R128, R138, R148, R158, R168, R178, R188, R198, R208, R218, R228, R238, R248, R258, R268, R278, R288, R298: 330; 0603
R15, R19, R29, R39, R49, R59, R69, R79, R89, R99, R109, R119, R129, R139, R149, R159, R169, R179, R189, R199, R209, R219, R229, R239, R249, R259, R269, R279, R289, R299: 0.12; 1206
S, S1, S2, S3, S4, S5, S6, S7, S8, S9, S10, S11, S12, S13, S14, S15, S16, S17, S18, S19, S20, S21, S22, S23, S24, S25, S26, S27, S28, S29: JUMPER-SMT_2_NC_TRACE_SILK; SMT-JUMPER_2_NC_TRACE_SILK
U1, U2, U3, U4, U5, U6, U7, U8, U9, U10, U11, U12, U13, U14, U15, U16, U17, U18, U19, U20, U21, U22, U23, U24, U25, U26, U27, U28, U29, U30: TMC6300; QFN-20
U$1, U$5, U$28, U$38, U$51, U$63, U$76, U$88, U$101, U$113, U$126, U$138, U$151, U$163, U$176, U$188, U$201, U$213, U$226, U$238, U$251, U$263, U$276, U$288, U$301, U$313, U$326, U$338, U$351, U$363, U$376, U$388, U$401, U$413, U$426, U$438, U$451, U$463, U$476, U$488, U$501, U$513, U$526, U$538, U$551, U$563, U$576, U$588, U$601, U$613, U$626, U$638, U$651, U$663, U$676, U$688, U$701, U$713, U$726, U$738: #GND#1
U$2, U$48, U$73, U$98, U$123, U$148, U$173, U$198, U$223, U$248, U$273, U$298, U$323, U$348, U$373, U$398, U$423, U$448, U$473, U$498, U$523, U$548, U$573, U$598, U$623, U$648, U$673, U$698, U$723, U$748: #SEN#0
U$3, U$49, U$74, U$99, U$124, U$149, U$174, U$199, U$224, U$249, U$274, U$299, U$324, U$349, U$374, U$399, U$424, U$449, U$474, U$499, U$524, U$549, U$574, U$599, U$624, U$649, U$674, U$699, U$724, U$749: #DIAG#0
U$4, U$50, U$75, U$100, U$125, U$150, U$175, U$200, U$225, U$250, U$275, U$300, U$325, U$350, U$375, U$400, U$425, U$450, U$475, U$500, U$525, U$550, U$575, U$600, U$625, U$650, U$675, U$700, U$725, U$750: TMC630063003454
U$6, U$12, U$52, U$77, U$102, U$127, U$152, U$177, U$202, U$227, U$252, U$277, U$302, U$327, U$352, U$377, U$402, U$427, U$452, U$477, U$502, U$527, U$552, U$577, U$602, U$627, U$652, U$677, U$702, U$727: #VCP#0
U$7, U$13, U$53, U$78, U$103, U$128, U$153, U$178, U$203, U$228, U$253, U$278, U$303, U$328, U$353, U$378, U$403, U$428, U$453, U$478, U$503, U$528, U$553, U$578, U$603, U$628, U$653, U$678, U$703, U$728: #VIO#1
U$8, U$14, U$16, U$18, U$54, U$57, U$79, U$82, U$104, U$107, U$129, U$132, U$154, U$157, U$179, U$182, U$204, U$207, U$229, U$232, U$254, U$257, U$279, U$282, U$304, U$307, U$329, U$332, U$354, U$357, U$379, U$382, U$404, U$407, U$429, U$432, U$454, U$457, U$479, U$482, U$504, U$507, U$529, U$532, U$554, U$557, U$579, U$582, U$604, U$607, U$629, U$632, U$654, U$657, U$679, U$682, U$704, U$707, U$729, U$732: D0
U$9, U$39, U$64, U$89, U$114, U$139, U$164, U$189, U$214, U$239, U$264, U$289, U$314, U$339, U$364, U$389, U$414, U$439, U$464, U$489, U$514, U$539, U$564, U$589, U$614, U$639, U$664, U$689, U$714, U$739: #U#6
U$10, U$20, U$26, U$29, U$55, U$59, U$80, U$84, U$105, U$109, U$130, U$134, U$155, U$159, U$180, U$184, U$205, U$209, U$230, U$234, U$255, U$259, U$280, U$284, U$305, U$309, U$330, U$334, U$355, U$359, U$380, U$384, U$405, U$409, U$430, U$434, U$455, U$459, U$480, U$484, U$505, U$509, U$530, U$534, U$555, U$559, U$580, U$584, U$605, U$609, U$630, U$634, U$655, U$659, U$680, U$684, U$705, U$709, U$730, U$734: V2
U$11, U$17, U$19, U$27, U$56, U$58, U$81, U$83, U$106, U$108, U$131, U$133, U$156, U$158, U$181, U$183, U$206, U$208, U$231, U$233, U$256, U$258, U$281, U$283, U$306, U$308, U$331, U$333, U$356, U$358, U$381, U$383, U$406, U$408, U$431, U$433, U$456, U$458, U$481, U$483, U$506, U$508, U$531, U$533, U$556, U$558, U$581, U$583, U$606, U$608, U$631, U$633, U$656, U$658, U$681, U$683, U$706, U$708, U$731, U$733: S1
U$15, U$35, U$60, U$85, U$110, U$135, U$160, U$185, U$210, U$235, U$260, U$285, U$310, U$335, U$360, U$385, U$410, U$435, U$460, U$485, U$510, U$535, U$560, U$585, U$610, U$635, U$660, U$685, U$710, U$735: 63001
U$21, U$40, U$65, U$90, U$115, U$140, U$165, U$190, U$215, U$240, U$265, U$290, U$315, U$340, U$365, U$390, U$415, U$440, U$465, U$490, U$515, U$540, U$565, U$590, U$615, U$640, U$665, U$690, U$715, U$740: #UH#5
U$22, U$41, U$66, U$91, U$116, U$141, U$166, U$191, U$216, U$241, U$266, U$291, U$316, U$341, U$366, U$391, U$416, U$441, U$466, U$491, U$516, U$541, U$566, U$591, U$616, U$641, U$666, U$691, U$716, U$741: #UL#4
U$23, U$36, U$61, U$86, U$111, U$136, U$161, U$186, U$211, U$236, U$261, U$286, U$311, U$336, U$361, U$386, U$411, U$436, U$461, U$486, U$511, U$536, U$561, U$586, U$611, U$636, U$661, U$686, U$711, U$736: TMC0
U$24, U$37, U$62, U$87, U$112, U$137, U$162, U$187, U$212, U$237, U$262, U$287, U$312, U$337, U$362, U$387, U$412, U$437, U$462, U$487, U$512, U$537, U$562, U$587, U$612, U$637, U$662, U$687, U$712, U$737: #VIN#0
U$25, U$42, U$67, U$92, U$117, U$142, U$167, U$192, U$217, U$242, U$267, U$292, U$317, U$342, U$367, U$392, U$417, U$442, U$467, U$492, U$517, U$542, U$567, U$592, U$617, U$642, U$667, U$692, U$717, U$742: #V#7
U$30, U$43, U$68, U$93, U$118, U$143, U$168, U$193, U$218, U$243, U$268, U$293, U$318, U$343, U$368, U$393, U$418, U$443, U$468, U$493, U$518, U$543, U$568, U$593, U$618, U$643, U$668, U$693, U$718, U$743: #VH#2
U$31, U$44, U$69, U$94, U$119, U$144, U$169, U$194, U$219, U$244, U$269, U$294, U$319, U$344, U$369, U$394, U$419, U$444, U$469, U$494, U$519, U$544, U$569, U$594, U$619, U$644, U$669, U$694, U$719, U$744: #VL#3
U$32, U$45, U$70, U$95, U$120, U$145, U$170, U$195, U$220, U$245, U$270, U$295, U$320, U$345, U$370, U$395, U$420, U$445, U$470, U$495, U$520, U$545, U$570, U$595, U$620, U$645, U$670, U$695, U$720, U$745: #W#8
U$33, U$46, U$71, U$96, U$121, U$146, U$171, U$196, U$221, U$246, U$271, U$296, U$321, U$346, U$371, U$396, U$421, U$446, U$471, U$496, U$521, U$546, U$571, U$596, U$621, U$646, U$671, U$696, U$721, U$746: #WH#1
U$34, U$47, U$72, U$97, U$122, U$147, U$172, U$197, U$222, U$247, U$272, U$297, U$322, U$347, U$372, U$397, U$422, U$447, U$472, U$497, U$522, U$547, U$572, U$597, U$622, U$647, U$672, U$697, U$722, U$747: #WL#0
V, V1, V2, V3, V4, V5, V6, V7, V8, V9, V10, V11, V12, V13, V14, V15, V16, V17, V18, V19, V20, V21, V22, V23, V24, V25, V26, V27, V28, V29: JUMPER-SMT_2_NC_TRACE_SILK; SMT-JUMPER_2_NC_TRACE_SILK

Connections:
DIAG: D.2, J2.7, U1.12
DIAG1: D5.2, J4.7, U2.12
DIAG2: D9.2, J6.7, U3.12
DIAG3: D13.2, J8.7, U4.12
DIAG4: D17.2, J10.7, U5.12
DIAG5: D21.2, J12.7, U6.12
DIAG6: D25.2, J14.7, U7.12
DIAG7: D29.2, J16.7, U8.12
DIAG8: D33.2, J18.7, U9.12
DIAG9: D37.2, J20.7, U10.12
DIAG10: D41.2, J22.7, U11.12
DIAG11: D45.2, J24.7, U12.12
DIAG12: D49.2, J26.7, U13.12
DIAG13: D53.2, J28.7, U14.12
DIAG14: D57.2, J30.7, U15.12
DIAG15: D61.2, J32.7, U16.12
DIAG16: D65.2, J34.7, U17.12
DIAG17: D69.2, J36.7, U18.12
DIAG18: D73.2, J38.7, U19.12
DIAG19: D77.2, J40.7, U20.12
DIAG20: D81.2, J42.7, U21.12
DIAG21: D85.2, J44.7, U22.12
DIAG22: D89.2, J46.7, U23.12
DIAG23: D93.2, J48.7, U24.12
DIAG24: D97.2, J50.7, U25.12
DIAG25: D101.2, J52.7, U26.12
DIAG26: D105.2, J54.7, U27.12
DIAG27: D109.2, J56.7, U28.12
DIAG28: D113.2, J58.7, U29.12
DIAG29: D117.2, J60.7, U30.12
GND: C3.2, C4.2, C5.2, D1.C, J2.2, J2.8, R1.1, R5.1, R6.1, R7.1, R8.1, R9.1, R10.1, R14.1, R15.1, U1.8, U1.9, U1.14, U1.PAD
GND1: C1.2, C2.2, C6.2, D2.C, J4.2, J4.8, R4.1, R11.1, R12.1, R13.1, R16.1, R17.1, R18.1, R19.1, R20.1, U2.8, U2.9, U2.14, U2.PAD
GND2: C7.2, C8.2, C9.2, D8.C, J6.2, J6.8, R22.1, R23.1, R24.1, R25.1, R26.1, R27.1, R28.1, R29.1, R30.1, U3.8, U3.9, U3.14, U3.PAD
GND3: C10.2, C11.2, C12.2, D12.C, J8.2, J8.8, R32.1, R33.1, R34.1, R35.1, R36.1, R37.1, R38.1, R39.1, R40.1, U4.8, U4.9, U4.14, U4.PAD
GND4: C13.2, C14.2, C15.2, D16.C, J10.2, J10.8, R42.1, R43.1, R44.1, R45.1, R46.1, R47.1, R48.1, R49.1, R50.1, U5.8, U5.9, U5.14, U5.PAD
GND5: C16.2, C17.2, C18.2, D20.C, J12.2, J12.8, R52.1, R53.1, R54.1, R55.1, R56.1, R57.1, R58.1, R59.1, R60.1, U6.8, U6.9, U6.14, U6.PAD
GND6: C19.2, C20.2, C21.2, D24.C, J14.2, J14.8, R62.1, R63.1, R64.1, R65.1, R66.1, R67.1, R68.1, R69.1, R70.1, U7.8, U7.9, U7.14, U7.PAD
GND7: C22.2, C23.2, C24.2, D28.C, J16.2, J16.8, R72.1, R73.1, R74.1, R75.1, R76.1, R77.1, R78.1, R79.1, R80.1, U8.8, U8.9, U8.14, U8.PAD
GND8: C25.2, C26.2, C27.2, D32.C, J18.2, J18.8, R82.1, R83.1, R84.1, R85.1, R86.1, R87.1, R88.1, R89.1, R90.1, U9.8, U9.9, U9.14, U9.PAD
GND9: C28.2, C29.2, C30.2, D36.C, J20.2, J20.8, R92.1, R93.1, R94.1, R95.1, R96.1, R97.1, R98.1, R99.1, R100.1, U10.8, U10.9, U10.14, U10.PAD
GND10: C31.2, C32.2, C33.2, D40.C, J22.2, J22.8, R102.1, R103.1, R104.1, R105.1, R106.1, R107.1, R108.1, R109.1, R110.1, U11.8, U11.9, U11.14, U11.PAD
GND11: C34.2, C35.2, C36.2, D44.C, J24.2, J24.8, R112.1, R113.1, R114.1, R115.1, R116.1, R117.1, R118.1, R119.1, R120.1, U12.8, U12.9, U12.14, U12.PAD
GND12: C37.2, C38.2, C39.2, D48.C, J26.2, J26.8, R122.1, R123.1, R124.1, R125.1, R126.1, R127.1, R128.1, R129.1, R130.1, U13.8, U13.9, U13.14, U13.PAD
GND13: C40.2, C41.2, C42.2, D52.C, J28.2, J28.8, R132.1, R133.1, R134.1, R135.1, R136.1, R137.1, R138.1, R139.1, R140.1, U14.8, U14.9, U14.14, U14.PAD
GND14: C43.2, C44.2, C45.2, D56.C, J30.2, J30.8, R142.1, R143.1, R144.1, R145.1, R146.1, R147.1, R148.1, R149.1, R150.1, U15.8, U15.9, U15.14, U15.PAD
GND15: C46.2, C47.2, C48.2, D60.C, J32.2, J32.8, R152.1, R153.1, R154.1, R155.1, R156.1, R157.1, R158.1, R159.1, R160.1, U16.8, U16.9, U16.14, U16.PAD
GND16: C49.2, C50.2, C51.2, D64.C, J34.2, J34.8, R162.1, R163.1, R164.1, R165.1, R166.1, R167.1, R168.1, R169.1, R170.1, U17.8, U17.9, U17.14, U17.PAD
GND17: C52.2, C53.2, C54.2, D68.C, J36.2, J36.8, R172.1, R173.1, R174.1, R175.1, R176.1, R177.1, R178.1, R179.1, R180.1, U18.8, U18.9, U18.14, U18.PAD
GND18: C55.2, C56.2, C57.2, D72.C, J38.2, J38.8, R182.1, R183.1, R184.1, R185.1, R186.1, R187.1, R188.1, R189.1, R190.1, U19.8, U19.9, U19.14, U19.PAD
GND19: C58.2, C59.2, C60.2, D76.C, J40.2, J40.8, R192.1, R193.1, R194.1, R195.1, R196.1, R197.1, R198.1, R199.1, R200.1, U20.8, U20.9, U20.14, U20.PAD
GND20: C61.2, C62.2, C63.2, D80.C, J42.2, J42.8, R202.1, R203.1, R204.1, R205.1, R206.1, R207.1, R208.1, R209.1, R210.1, U21.8, U21.9, U21.14, U21.PAD
GND21: C64.2, C65.2, C66.2, D84.C, J44.2, J44.8, R212.1, R213.1, R214.1, R215.1, R216.1, R217.1, R218.1, R219.1, R220.1, U22.8, U22.9, U22.14, U22.PAD
GND22: C67.2, C68.2, C69.2, D88.C, J46.2, J46.8, R222.1, R223.1, R224.1, R225.1, R226.1, R227.1, R228.1, R229.1, R230.1, U23.8, U23.9, U23.14, U23.PAD
GND23: C70.2, C71.2, C72.2, D92.C, J48.2, J48.8, R232.1, R233.1, R234.1, R235.1, R236.1, R237.1, R238.1, R239.1, R240.1, U24.8, U24.9, U24.14, U24.PAD
GND24: C73.2, C74.2, C75.2, D96.C, J50.2, J50.8, R242.1, R243.1, R244.1, R245.1, R246.1, R247.1, R248.1, R249.1, R250.1, U25.8, U25.9, U25.14, U25.PAD
GND25: C76.2, C77.2, C78.2, D100.C, J52.2, J52.8, R252.1, R253.1, R254.1, R255.1, R256.1, R257.1, R258.1, R259.1, R260.1, U26.8, U26.9, U26.14, U26.PAD
GND26: C79.2, C80.2, C81.2, D104.C, J54.2, J54.8, R262.1, R263.1, R264.1, R265.1, R266.1, R267.1, R268.1, R269.1, R270.1, U27.8, U27.9, U27.14, U27.PAD
GND27: C82.2, C83.2, C84.2, D108.C, J56.2, J56.8, R272.1, R273.1, R274.1, R275.1, R276.1, R277.1, R278.1, R279.1, R280.1, U28.8, U28.9, U28.14, U28.PAD
GND28: C85.2, C86.2, C87.2, D112.C, J58.2, J58.8, R282.1, R283.1, R284.1, R285.1, R286.1, R287.1, R288.1, R289.1, R290.1, U29.8, U29.9, U29.14, U29.PAD
GND29: C88.2, C89.2, C90.2, D116.C, J60.2, J60.8, R292.1, R293.1, R294.1, R295.1, R296.1, R297.1, R298.1, R299.1, R300.1, U30.8, U30.9, U30.14, U30.PAD
unnamed: R3.2, V.1
unnamed: R2.2, V1.1
unnamed: D2.A, R2.1
unnamed: D1.A, R3.1
unnamed: D3.A, S.1
unnamed: C5.1, U1.13
unnamed: C6.1, U2.13
unnamed: D5.1, D7.A
unnamed: D.1, D4.A
unnamed: D3.C, R1.2
unnamed: D6.A, S1.1
unnamed: D4.C, R14.2
unnamed: D7.C, R18.2
unnamed: D6.C, R20.2
unnamed: R21.2, V2.1
unnamed: D8.A, R21.1
unnamed: C9.1, U3.13
unnamed: D9.1, D11.A
unnamed: D10.A, S2.1
unnamed: D11.C, R28.2
unnamed: D10.C, R30.2
unnamed: R31.2, V3.1
unnamed: D12.A, R31.1
unnamed: C12.1, U4.13
unnamed: D13.1, D15.A
unnamed: D14.A, S3.1
unnamed: D15.C, R38.2
unnamed: D14.C, R40.2
unnamed: R41.2, V4.1
unnamed: D16.A, R41.1
unnamed: C15.1, U5.13
unnamed: D17.1, D19.A
unnamed: D18.A, S4.1
unnamed: D19.C, R48.2
unnamed: D18.C, R50.2
unnamed: R51.2, V5.1
unnamed: D20.A, R51.1
unnamed: C18.1, U6.13
unnamed: D21.1, D23.A
unnamed: D22.A, S5.1
unnamed: D23.C, R58.2
unnamed: D22.C, R60.2
unnamed: R61.2, V6.1
unnamed: D24.A, R61.1
unnamed: C21.1, U7.13
unnamed: D25.1, D27.A
unnamed: D26.A, S6.1
unnamed: D27.C, R68.2
unnamed: D26.C, R70.2
unnamed: R71.2, V7.1
unnamed: D28.A, R71.1
unnamed: C24.1, U8.13
unnamed: D29.1, D31.A
unnamed: D30.A, S7.1
unnamed: D31.C, R78.2
unnamed: D30.C, R80.2
unnamed: R81.2, V8.1
unnamed: D32.A, R81.1
unnamed: C27.1, U9.13
unnamed: D33.1, D35.A
unnamed: D34.A, S8.1
unnamed: D35.C, R88.2
unnamed: D34.C, R90.2
unnamed: R91.2, V9.1
unnamed: D36.A, R91.1
unnamed: C30.1, U10.13
unnamed: D37.1, D39.A
unnamed: D38.A, S9.1
unnamed: D39.C, R98.2
unnamed: D38.C, R100.2
unnamed: R101.2, V10.1
unnamed: D40.A, R101.1
unnamed: C33.1, U11.13
unnamed: D41.1, D43.A
unnamed: D42.A, S10.1
unnamed: D43.C, R108.2
unnamed: D42.C, R110.2
unnamed: R111.2, V11.1
unnamed: D44.A, R111.1
unnamed: C36.1, U12.13
unnamed: D45.1, D47.A
unnamed: D46.A, S11.1
unnamed: D47.C, R118.2
unnamed: D46.C, R120.2
unnamed: R121.2, V12.1
unnamed: D48.A, R121.1
unnamed: C39.1, U13.13
unnamed: D49.1, D51.A
unnamed: D50.A, S12.1
unnamed: D51.C, R128.2
unnamed: D50.C, R130.2
unnamed: R131.2, V13.1
unnamed: D52.A, R131.1
unnamed: C42.1, U14.13
unnamed: D53.1, D55.A
unnamed: D54.A, S13.1
unnamed: D55.C, R138.2
unnamed: D54.C, R140.2
unnamed: R141.2, V14.1
unnamed: D56.A, R141.1
unnamed: C45.1, U15.13
unnamed: D57.1, D59.A
unnamed: D58.A, S14.1
unnamed: D59.C, R148.2
unnamed: D58.C, R150.2
unnamed: R151.2, V15.1
unnamed: D60.A, R151.1
unnamed: C48.1, U16.13
unnamed: D61.1, D63.A
unnamed: D62.A, S15.1
unnamed: D63.C, R158.2
unnamed: D62.C, R160.2
unnamed: R161.2, V16.1
unnamed: D64.A, R161.1
unnamed: C51.1, U17.13
unnamed: D65.1, D67.A
unnamed: D66.A, S16.1
unnamed: D67.C, R168.2
unnamed: D66.C, R170.2
unnamed: R171.2, V17.1
unnamed: D68.A, R171.1
unnamed: C54.1, U18.13
unnamed: D69.1, D71.A
unnamed: D70.A, S17.1
unnamed: D71.C, R178.2
unnamed: D70.C, R180.2
unnamed: R181.2, V18.1
unnamed: D72.A, R181.1
unnamed: C57.1, U19.13
unnamed: D73.1, D75.A
unnamed: D74.A, S18.1
unnamed: D75.C, R188.2
unnamed: D74.C, R190.2
unnamed: R191.2, V19.1
unnamed: D76.A, R191.1
unnamed: C60.1, U20.13
unnamed: D77.1, D79.A
unnamed: D78.A, S19.1
unnamed: D79.C, R198.2
unnamed: D78.C, R200.2
unnamed: R201.2, V20.1
unnamed: D80.A, R201.1
unnamed: C63.1, U21.13
unnamed: D81.1, D83.A
unnamed: D82.A, S20.1
unnamed: D83.C, R208.2
unnamed: D82.C, R210.2
unnamed: R211.2, V21.1
unnamed: D84.A, R211.1
unnamed: C66.1, U22.13
unnamed: D85.1, D87.A
unnamed: D86.A, S21.1
unnamed: D87.C, R218.2
unnamed: D86.C, R220.2
unnamed: R221.2, V22.1
unnamed: D88.A, R221.1
unnamed: C69.1, U23.13
unnamed: D89.1, D91.A
unnamed: D90.A, S22.1
unnamed: D91.C, R228.2
unnamed: D90.C, R230.2
unnamed: R231.2, V23.1
unnamed: D92.A, R231.1
unnamed: C72.1, U24.13
unnamed: D93.1, D95.A
unnamed: D94.A, S23.1
unnamed: D95.C, R238.2
unnamed: D94.C, R240.2
unnamed: R241.2, V24.1
unnamed: D96.A, R241.1
unnamed: C75.1, U25.13
unnamed: D97.1, D99.A
unnamed: D98.A, S24.1
unnamed: D99.C, R248.2
unnamed: D98.C, R250.2
unnamed: R251.2, V25.1
unnamed: D100.A, R251.1
unnamed: C78.1, U26.13
unnamed: D101.1, D103.A
unnamed: D102.A, S25.1
unnamed: D103.C, R258.2
unnamed: D102.C, R260.2
unnamed: R261.2, V26.1
unnamed: D104.A, R261.1
unnamed: C81.1, U27.13
unnamed: D105.1, D107.A
unnamed: D106.A, S26.1
unnamed: D107.C, R268.2
unnamed: D106.C, R270.2
unnamed: R271.2, V27.1
unnamed: D108.A, R271.1
unnamed: C84.1, U28.13
unnamed: D109.1, D111.A
unnamed: D110.A, S27.1
unnamed: D111.C, R278.2
unnamed: D110.C, R280.2
unnamed: R281.2, V28.1
unnamed: D112.A, R281.1
unnamed: C87.1, U29.13
unnamed: D113.1, D115.A
unnamed: D114.A, S28.1
unnamed: D115.C, R288.2
unnamed: D114.C, R290.2
unnamed: R291.2, V29.1
unnamed: D116.A, R291.1
unnamed: C90.1, U30.13
unnamed: D117.1, D119.A
unnamed: D118.A, S29.1
unnamed: D119.C, R298.2
unnamed: D118.C, R300.2
SENSE: J2.6, R15.2, U1.16, U1.20
SENSE1: J4.6, R19.2, U2.16, U2.20
SENSE2: J6.6, R29.2, U3.16, U3.20
SENSE3: J8.6, R39.2, U4.16, U4.20
SENSE4: J10.6, R49.2, U5.16, U5.20
SENSE5: J12.6, R59.2, U6.16, U6.20
SENSE6: J14.6, R69.2, U7.16, U7.20
SENSE7: J16.6, R79.2, U8.16, U8.20
SENSE8: J18.6, R89.2, U9.16, U9.20
SENSE9: J20.6, R99.2, U10.16, U10.20
SENSE10: J22.6, R109.2, U11.16, U11.20
SENSE11: J24.6, R119.2, U12.16, U12.20
SENSE12: J26.6, R129.2, U13.16, U13.20
SENSE13: J28.6, R139.2, U14.16, U14.20
SENSE14: J30.6, R149.2, U15.16, U15.20
SENSE15: J32.6, R159.2, U16.16, U16.20
SENSE16: J34.6, R169.2, U17.16, U17.20
SENSE17: J36.6, R179.2, U18.16, U18.20
SENSE18: J38.6, R189.2, U19.16, U19.20
SENSE19: J40.6, R199.2, U20.16, U20.20
SENSE20: J42.6, R209.2, U21.16, U21.20
SENSE21: J44.6, R219.2, U22.16, U22.20
SENSE22: J46.6, R229.2, U23.16, U23.20
SENSE23: J48.6, R239.2, U24.16, U24.20
SENSE24: J50.6, R249.2, U25.16, U25.20
SENSE25: J52.6, R259.2, U26.16, U26.20
SENSE26: J54.6, R269.2, U27.16, U27.20
SENSE27: J56.6, R279.2, U28.16, U28.20
SENSE28: J58.6, R289.2, U29.16, U29.20
SENSE29: J60.6, R299.2, U30.16, U30.20
U: J2.3, U1.15
U1: J4.3, U2.15
U2: J6.3, U3.15
U3: J8.3, U4.15
U4: J10.3, U5.15
U5: J12.3, U6.15
U6: J14.3, U7.15
U7: J16.3, U8.15
U8: J18.3, U9.15
U9: J20.3, U10.15
U10: J22.3, U11.15
U11: J24.3, U12.15
U12: J26.3, U13.15
U13: J28.3, U14.15
U14: J30.3, U15.15
U15: J32.3, U16.15
U16: J34.3, U17.15
U17: J36.3, U18.15
U18: J38.3, U19.15
U19: J40.3, U20.15
U20: J42.3, U21.15
U21: J44.3, U22.15
U22: J46.3, U23.15
U23: J48.3, U24.15
U24: J50.3, U25.15
U25: J52.3, U26.15
U26: J54.3, U27.15
U27: J56.3, U28.15
U28: J58.3, U29.15
U29: J60.3, U30.15
UH: J1.6, R10.2, U1.3
UH1: J3.6, R17.2, U2.3
UH2: J5.6, R27.2, U3.3
UH3: J7.6, R37.2, U4.3
UH4: J9.6, R47.2, U5.3
UH5: J11.6, R57.2, U6.3
UH6: J13.6, R67.2, U7.3
UH7: J15.6, R77.2, U8.3
UH8: J17.6, R87.2, U9.3
UH9: J19.6, R97.2, U10.3
UH10: J21.6, R107.2, U11.3
UH11: J23.6, R117.2, U12.3
UH12: J25.6, R127.2, U13.3
UH13: J27.6, R137.2, U14.3
UH14: J29.6, R147.2, U15.3
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

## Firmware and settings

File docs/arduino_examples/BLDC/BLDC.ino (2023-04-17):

// Open loop motor control example
#include <SimpleFOC.h>


// BLDC motor & driver instance
// BLDCMotor motor = BLDCMotor(pole pair number);
BLDCMotor motor = BLDCMotor(7);
// BLDCDriver3PWM driver = BLDCDriver3PWM(pwmA, pwmB, pwmC, Enable(optional));
BLDCDriver6PWM driver = BLDCDriver6PWM(5, 6, 9,10, 3, 11);

// Stepper motor & driver instance
//StepperMotor motor = StepperMotor(50);
//StepperDriver4PWM driver = StepperDriver4PWM(9, 5, 10, 6,  8);


//target variable
float target_velocity = 6;

// // instantiate the commander
Commander command = Commander(Serial);
// void doTarget(char* cmd) { command.scalar(&target_velocity, cmd); }
// void doLimit(char* cmd) { command.scalar(&motor.voltage_limit, cmd); }

void setup() {

  // driver config
  // power supply voltage [V]
  driver.voltage_power_supply = 5;
  // limit the maximal dc voltage the driver can set
  // as a protection measure for the low-resistance motors
  // this value is fixed on startup
  driver.voltage_limit = 5;
  // pwm frequency to be used [Hz]
  // for atmega328 fixed to 32kHz
  // esp32/stm32/teensy configurable
  driver.pwm_frequency = 32000;
  

  driver.init();
  // link the motor and the driver
  motor.linkDriver(&driver);

  // limiting motor movements
  // limit the voltage to be set to the motor
  // start very low for high resistance motors
  // current = voltage / resistance, so try to be well under 1Amp
  motor.voltage_limit = 3;   // [V]
 
  // open loop control config
  motor.controller = MotionControlType::velocity_openloop;

  // init motor hardware
  motor.init();

  // add target command T
  // command.add('T', doTarget, "target velocity");
  // command.add('L', doLimit, "voltage limit");

  Serial.begin(115200);
  Serial.println("Motor ready!");
  Serial.println("Set target velocity [rad/s]");
  _delay(1000);

}

void loop() {

  // open loop velocity movement
  // using motor.voltage_limit and motor.velocity_limit
  motor.move(target_velocity);

  // user communication
  command.run();

  
}

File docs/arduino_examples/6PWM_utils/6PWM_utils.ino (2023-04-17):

// BLDC driver standalone example
#include <SimpleFOC.h>

// BLDC driver instance
BLDCDriver6PWM driver = BLDCDriver6PWM(5, 6, 9,10, 3, 11);

void setup() {

  // pwm frequency to be used [Hz]
  // for atmega328 fixed to 32kHz
  // esp32/stm32/teensy configurable
  driver.pwm_frequency = 32000;
  // power supply voltage [V]
  driver.voltage_power_supply = 5;
  // Max DC voltage allowed - default voltage_power_supply
  driver.voltage_limit = 5;
  // daad_zone [0,1] - default 0.02f - 2%
  driver.dead_zone = 0.05f;

  // driver init
  driver.init();

  // enable driver
  driver.enable();

  _delay(1000);
}

void loop() {
    driver.setPwm(5,0,0);
    _delay(1000);
    
    driver.setPwm(0,5,0);
    _delay(1000);
}

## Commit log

2023-02-14 Upload of initial SparkX files
    Files originally from Three_Phase_Motor_Driver-TM6300 in SparkX - no edits made yet
    [SparkFun_TMC6300_Breakout.brd, SparkFun_TMC6300_Breakout.sch]
2023-02-16 Updates for red review
    Added SparkFun logo, updated notes in schematic for user, changed blue LED resistor value, added OSHW logo, created panel and CAM files.
    [SparkFun_TMC6300_Breakout-Panel.GBL, SparkFun_TMC6300_Breakout-Panel.GBO, SparkFun_TMC6300_Breakout-Panel.GBP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]
2023-02-16 Changes made from design notes
    Changed vias to be all the same size, added paragraphs to S and D jumpers to explain what they're going to, added tRestrict layer to remove natural jumper between GND pads, fixed acid trap, added more GND vias for better heat sinking.
    [SparkFun_TMC6300_Breakout.brd, SparkFun_TMC6300_Breakout.sch]
2023-02-17 Updates to layout as per design review notes
    Added numbers to each layer to determine which layer it is in the copper, added dimensions for length and width of location of the main IC.
    [SparkFun_TMC6300_Breakout.brd]
2023-02-17 Updates from design review
    Changed tCream on the TMC6300 to be reduced by 5%, changed tRestrict polygon to a rectangle, adjusted C5 to match the datasheet for a good return path, adjusted some routing for less acid traps, adju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
    [SparkFun_TMC6300_Breakout.brd, SparkFun_TMC6300_Breakout.sch]
2023-02-20 Updated production files
    Re generated panelized files for ordering from design review changes
    [SparkFun_TMC6300_Breakout-Panel.brd, SparkFun_TMC6300_Breakout.brd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]
2023-02-20 Final updates before ordering
    Adjusted GND traces from TMC6300 for better connection, added paragraph for Power LED in schematic, updated panelized files for ordering.
    [SparkFun_TMC6300_Breakout-Panel.brd, SparkFun_TMC6300_Breakout.brd, SparkFun_TMC6300_Breakout.sch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]
2023-04-25 Update stylesheet
    Update to not display video_desc class when printing page
2023-06-16 Update hardware_overview.md
    Add current sense section
2024-06-06 Update LICENSE.md
    Remove carriage returns
    Fix link

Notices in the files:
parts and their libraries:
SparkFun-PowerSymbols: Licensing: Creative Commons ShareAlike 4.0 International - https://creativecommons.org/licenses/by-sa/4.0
